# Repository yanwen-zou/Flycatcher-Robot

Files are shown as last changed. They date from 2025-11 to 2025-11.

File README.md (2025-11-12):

# Flycatcher-Robot

> 愛すべきお客様に、ハートフルな今日と、最高の笑顔を。

<div style="text-align: center;">
  
</div>

This project is a replica of the Flycatcher Robot from the anime *Apocalypse Hotel*, designed as an open-source desktop-level quadruped robot. 

The majority of the hardware in this project consists of available standard items with links or 3D-printing parts. The CAD Model, BOM List, and assembly notes are provided.

## CAD Model

<div style="display: flex; justify-content: space-between;">
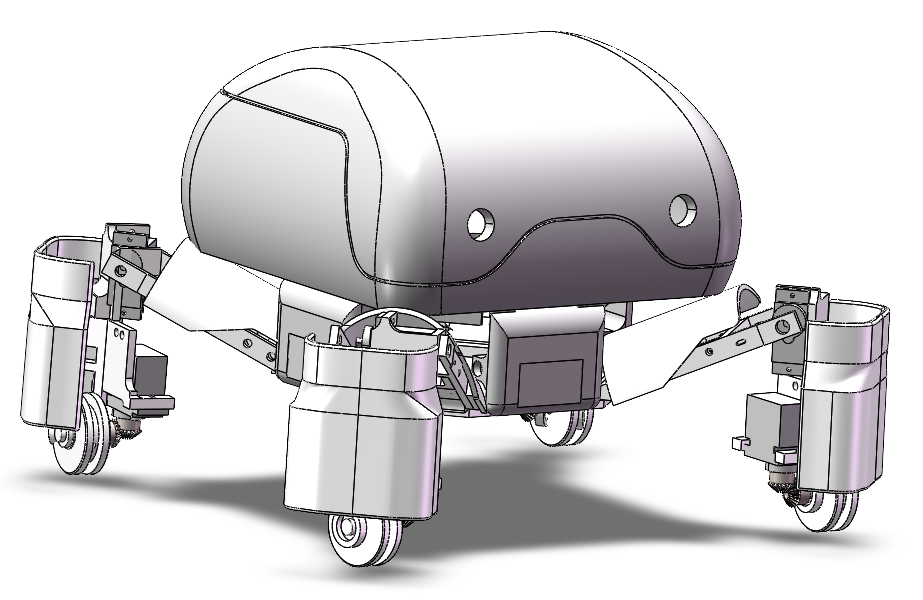
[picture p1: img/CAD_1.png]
  
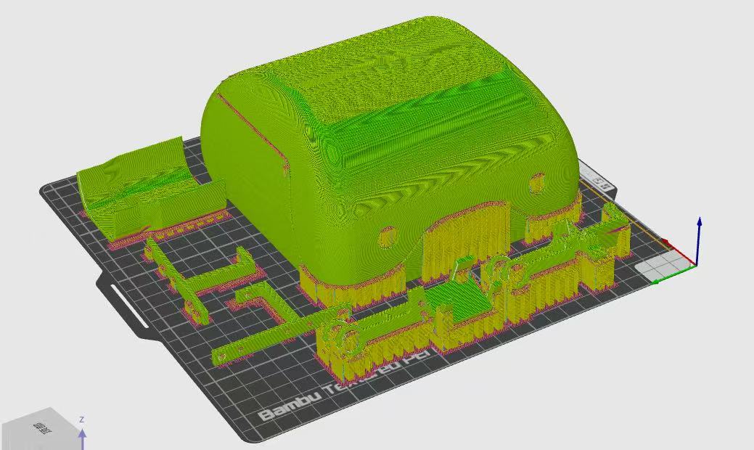
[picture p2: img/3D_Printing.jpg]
  
</div>

[Check the STL/STEP files here](https://github.com/yanwen-zou/Flycatcher-Robot/tree/main/model)

It is recommended to print using PLA and with tree support.

## BOM List

### Mechanical Parts

| Part Name | Link | Quantity | Price | Notes |
| --- | --- | --- | --- | ---  |
| mg90s servo 360 degrees | [Link](https://item.taobao.com/item.htm?id=939629018237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) | 4 | ¥54.00  | For wheels |
| mg90s servo 180 degrees | [Link](https://item.taobao.com/item.htm?id=939629018237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) | 4 | ¥51.60  | For leg joints |
| Mini bevel gear | [Link](https://item.taobao.com/item.htm?id=802831128052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) | 4 | ¥42.40  | 0.5 module, 20 teeth, 4mm shaft hole, fixed to the wheel and coupled with servos |
| Servo bevel gear | [Link](https://item.taobao.com/item.htm?id=924233815457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) | 4 | ¥42.40  | 0.5 module, 20 teeth, 4mm shaft hole, installed on the servo |
| Knurled nuts | [Link](https://item.taobao.com/item.htm?id=868299597594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) | 20 | ¥0.60  | 3*3*4.1 |
| Wheel | [Link](https://item.taobao.com/item.htm?id=851325146722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) | 4 | ¥44.00  | Outer diameter 30mm, groove width 4mm, thickness 10mm, width 6mm, inner hole |

### Electronics

| Part Name | Link | Quantity | Price | Notes |
| --- | --- | --- | --- | --- |
| 24-channel Servo Controller | [Link](https://item.taobao.com/item.htm?id=549015493634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) | 1 | ¥105.00 | For controlling servos |
| Joystick Controller | [Link](https://item.taobao.com/item.htm?id=549015493634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) | 1 | ¥41.60  | Includes 6P cable, receiver, and adapter board |
| Battery and Charger | [Link](https://item.taobao.com/item.htm?id=549015493634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) | 1 | ¥81.60  | Battery and charger |
| LED Light | [Link](https://item.taobao.com/item.htm?id=566087904384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) | 2 | ¥0.70 | Robot eyes |
| Shading Plate | [Link](https://detail.tmall.com/item.htm?id=924834751732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) | 2 | ¥2.40 | Applied inside the head part to make the eyes glow more naturally |

### For Color

| Part Name | Link | Quantity | Price | Notes |
| --- | --- | --- | --- | --- |
| Shell Paint | [Link](https://detail.tmall.com/item.htm?id=890818155017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) | 2 bottles  | ¥30.00  | Milk yellow |
| Primer | [Link](https://item.taobao.com/item.htm?id=886710659354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) | 2 bottles  | ¥47.60  | White |

Note 1: For the electronics, you can choose different control methods based on your needs.

Note 2: For developers in regions where Taobao is not accessible, you can refer to the size parameters and features to purchase similar accessories from platforms more accessible in your region. If there is significant demand, I will also compile a list of Amazon links in the future.

## Assembly Notes

1. Most screws used in the assembly are M2*10.

2. Due to the complexity of the mechanism and the precision of 3D printing, the head and body connection currently uses hot melt glue for attachment. It is recommended not to install the head until control logic debugging is complete. Feel free to modify the design based on the current model for a more refined joint mechanism or easier disassembly and contribute your changes!

3. The thigh-to-body connection parts require the insertion of two knurled nuts, which can be easily done using needle-nose pliers and a small hammer.

4. Similar to step 2, the leg shell is also attached using hot melt glue, so it is recommended to install it last.

## Wiring and Control

You should follow the official documentation from Zhongling to connect the servo wires to the control board and define the joystick controller interfaces in the software. 

It is important to note that for the four servos controlling the wheels, their wires need to be extended.

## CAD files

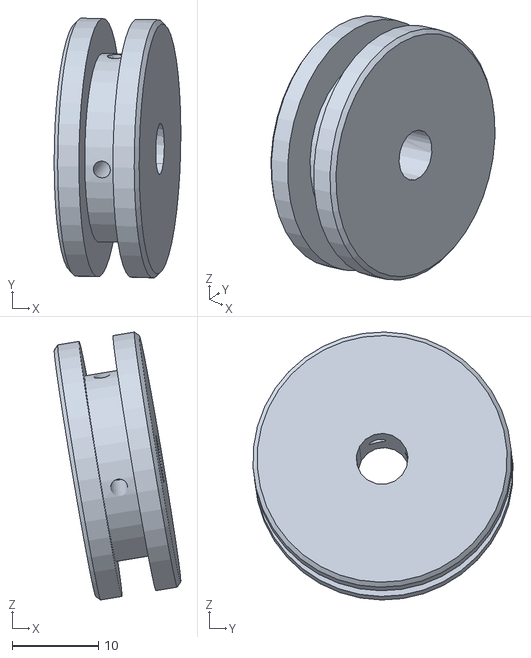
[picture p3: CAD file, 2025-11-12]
model/STL/FlycatcherRobot - wheel-8.STL
14.7 x 30.1 x 31.1

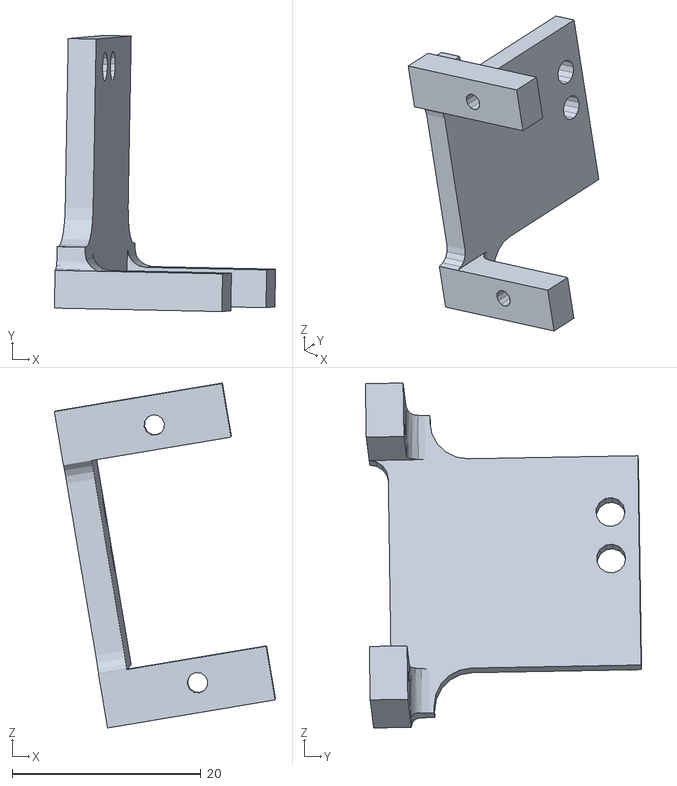
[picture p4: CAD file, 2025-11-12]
model/STL/FlycatcherRobot - mirror_gear_seat-3.STL
23.5 x 29.3 x 36.6

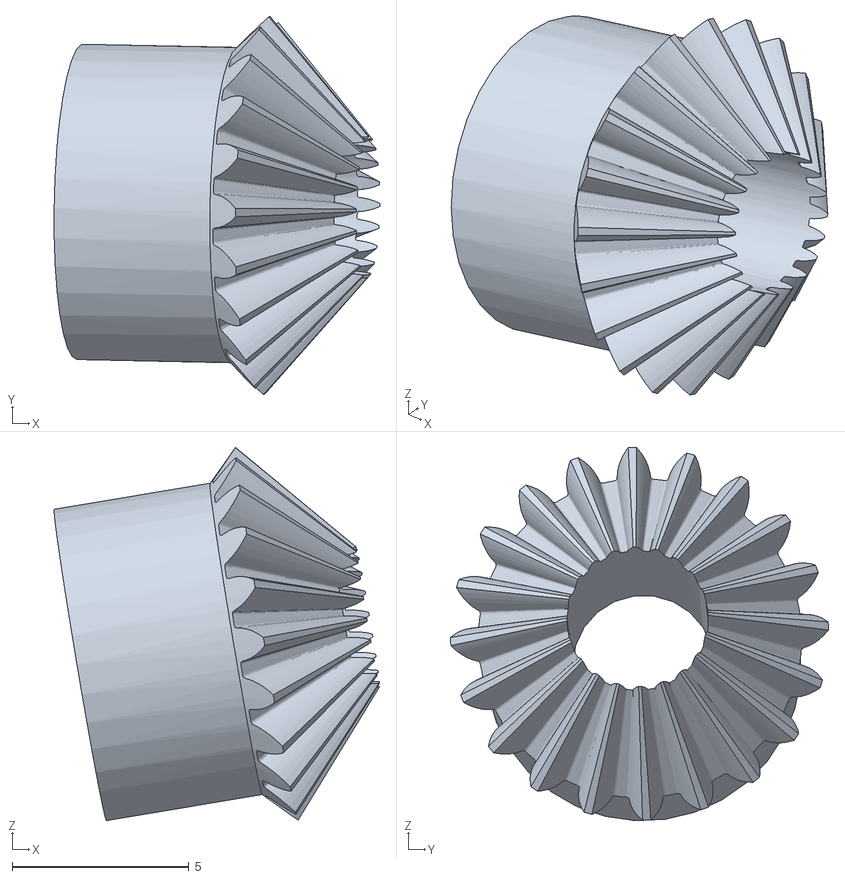
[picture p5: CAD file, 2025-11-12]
model/STL/FlycatcherRobot - straight bevel pinion_gb-10.STL
9.22 x 10.7 x 10.6

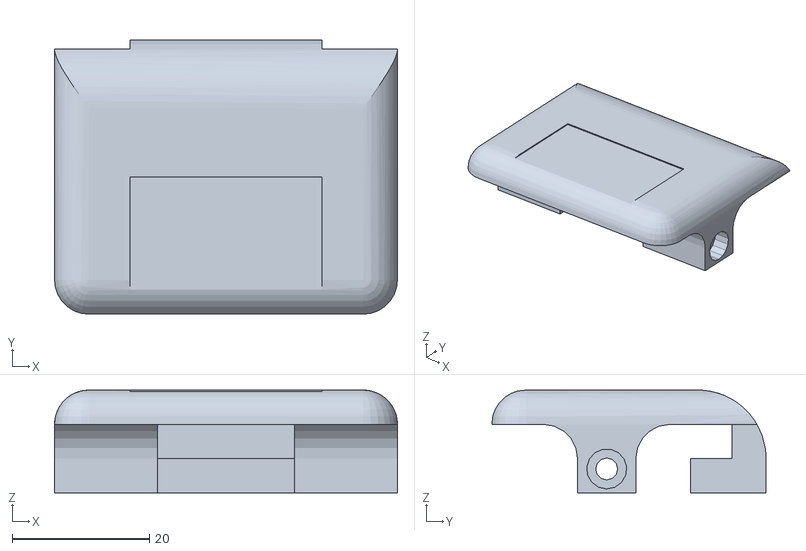
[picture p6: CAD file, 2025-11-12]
model/STL/FlycatcherRobot - body_shell-1.STL
50.0 x 40.0 x 15.0

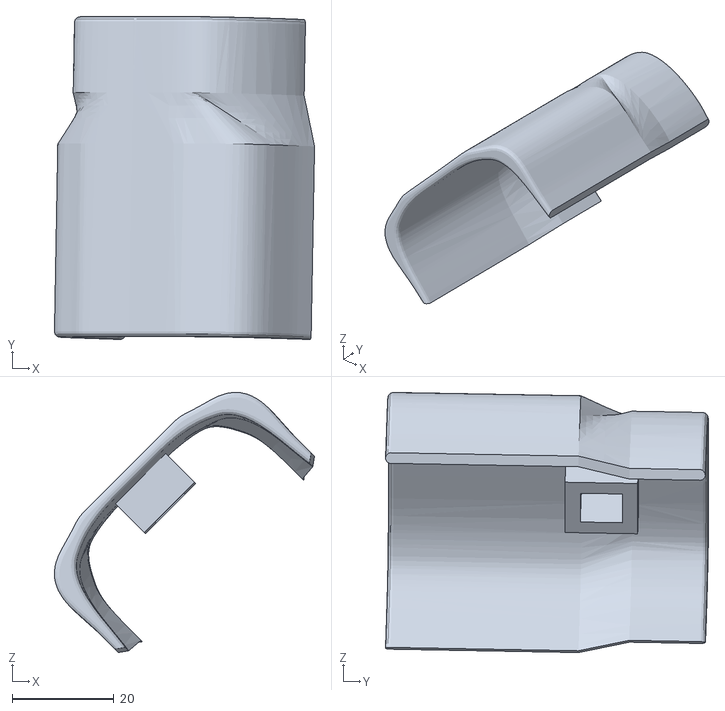
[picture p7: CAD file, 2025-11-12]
model/STL/FlycatcherRobot - shell_calf-1.STL
51.2 x 63.6 x 51.2

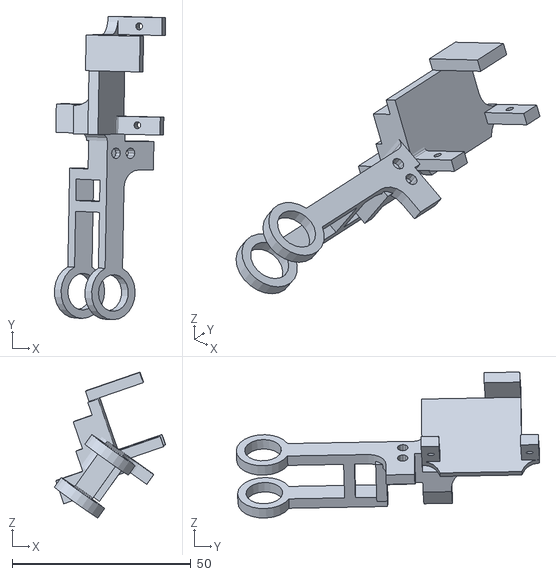
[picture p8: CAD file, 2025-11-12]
model/STL/FlycatcherRobot - mirror_calf-2.STL
31.1 x 85.0 x 40.9

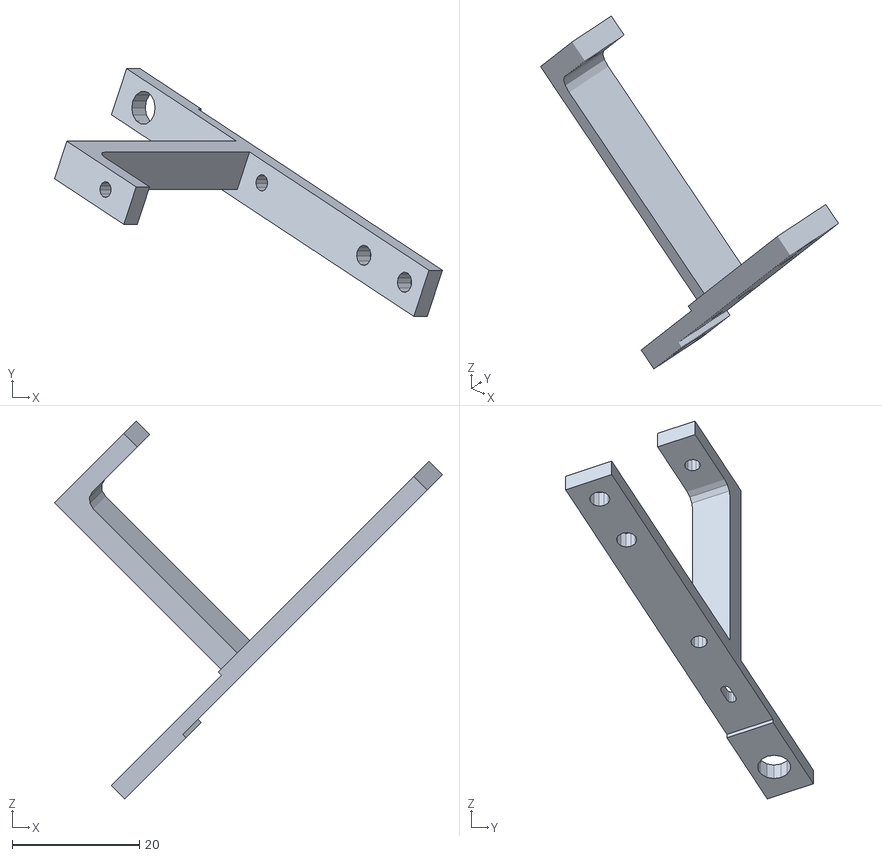
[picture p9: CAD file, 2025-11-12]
model/STL/FlycatcherRobot - leg_p2-8.STL
61.0 x 38.9 x 59.4

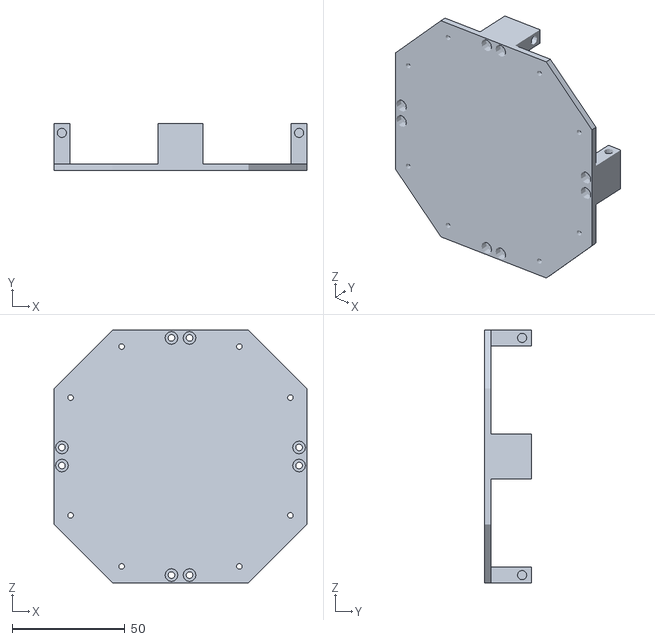
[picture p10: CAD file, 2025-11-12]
model/STL/FlycatcherRobot - middle_layer-1.STL
112.0 x 21.0 x 112.0

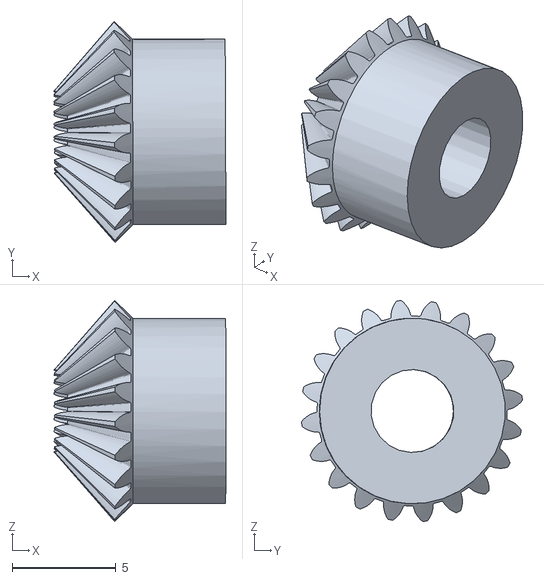
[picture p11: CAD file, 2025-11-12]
model/STL/FlycatcherRobot - straight bevel pinion_gb-8.STL
8.29 x 10.7 x 10.7

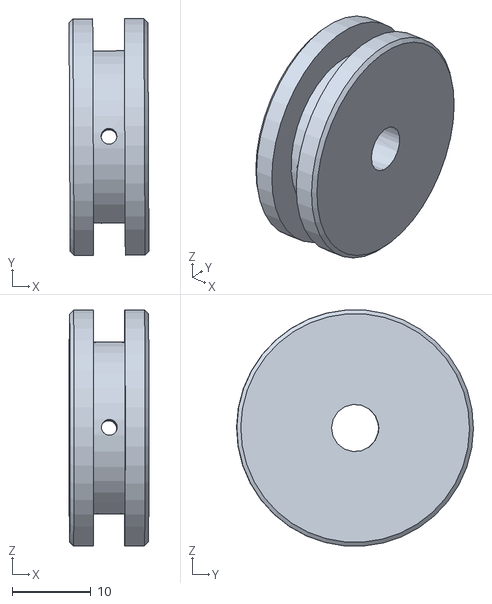
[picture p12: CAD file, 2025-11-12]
model/STL/FlycatcherRobot - wheel-7.STL
10.1 x 30.0 x 29.9

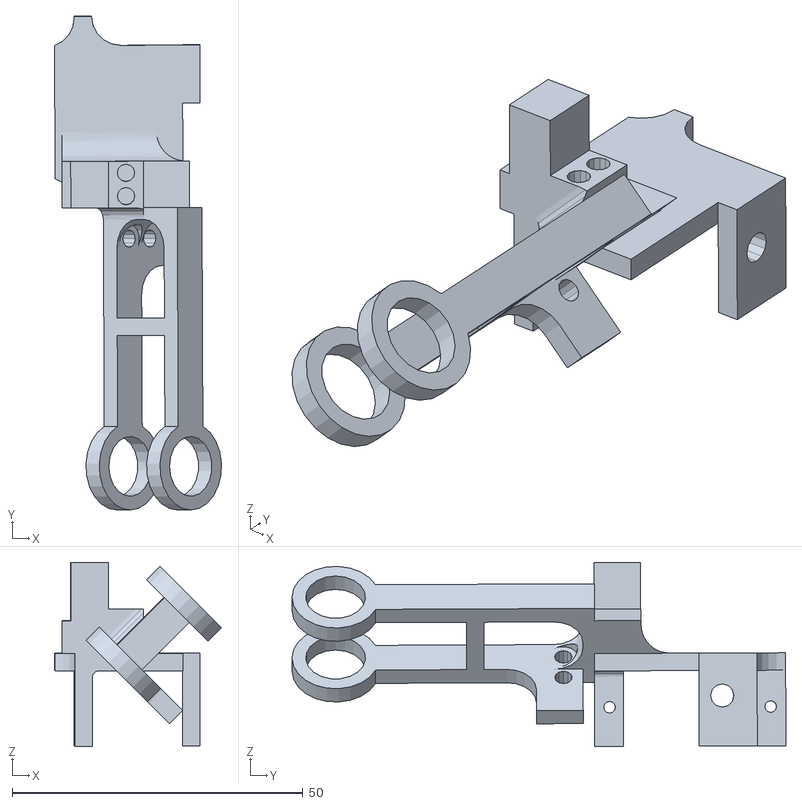
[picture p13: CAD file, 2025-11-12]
model/STL/FlycatcherRobot - calf-2.STL
28.7 x 84.9 x 31.7

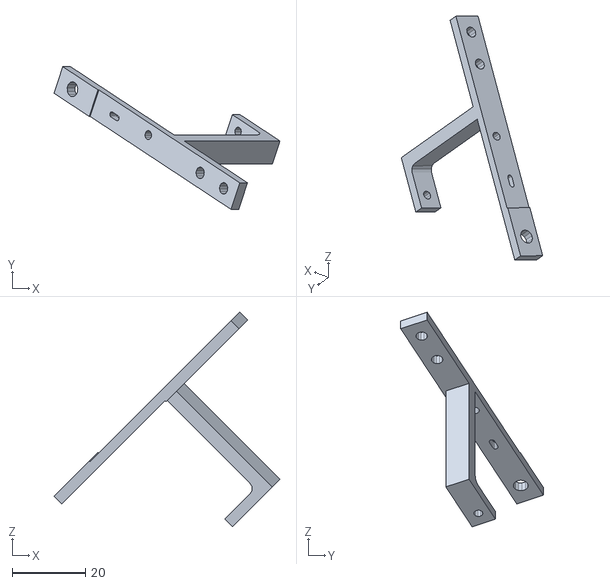
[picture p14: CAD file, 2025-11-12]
model/STL/FlycatcherRobot - leg_p1-10.STL
61.7 x 38.9 x 58.6

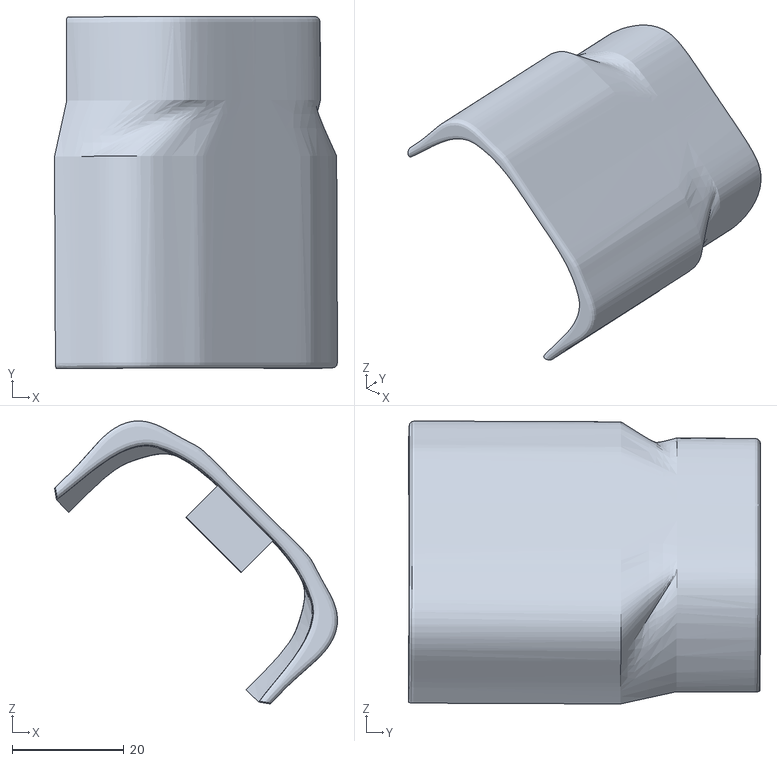
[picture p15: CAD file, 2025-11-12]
model/STL/FlycatcherRobot - shell_calf-2.STL
50.7 x 63.1 x 50.7

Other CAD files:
model/STL/FlycatcherRobot - body_shell-4.STL
model/STL/FlycatcherRobot - wheel-5.STL
model/STL/FlycatcherRobot - leg_p2-5.STL
model/STL/FlycatcherRobot - leg_p2-2.STL
model/STL/FlycatcherRobot - leg_p2-7.STL
model/STL/FlycatcherRobot - body_shell-2.STL
model/STL/FlycatcherRobot - body_shell-3.STL
model/STL/FlycatcherRobot - calf-1.STL
model/STL/FlycatcherRobot - gear_seat-1.STL
model/STL/FlycatcherRobot - gear_seat-4.STL
model/STL/FlycatcherRobot - head-1.STL
model/STL/FlycatcherRobot - leg_p1-7.STL
model/STL/FlycatcherRobot - leg_p1-8.STL
model/STL/FlycatcherRobot - leg_p1-9.STL
model/STL/FlycatcherRobot - leg_shell-1.STL
model/STL/FlycatcherRobot - leg_shell-5.STL
model/STL/FlycatcherRobot - leg_shell-7.STL
model/STL/FlycatcherRobot - leg_shell-8.STL
model/STL/FlycatcherRobot - leg_support-1.STL
model/STL/FlycatcherRobot - leg_support-2.STL
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
